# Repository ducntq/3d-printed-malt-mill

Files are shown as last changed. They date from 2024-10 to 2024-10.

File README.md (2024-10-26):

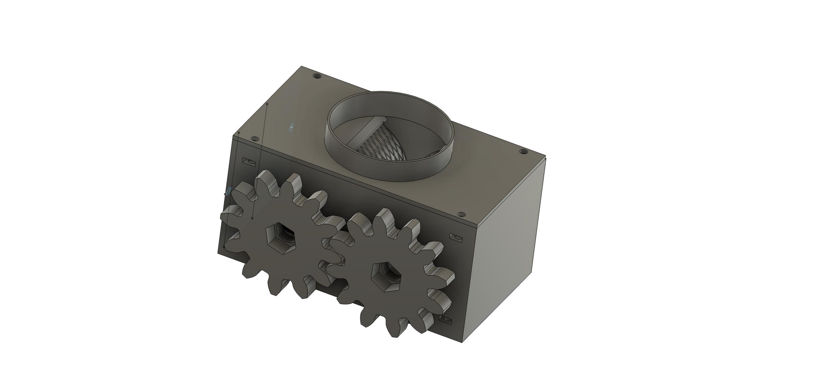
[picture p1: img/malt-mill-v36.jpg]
Malt Mill


# 3D Printer Malt Mill

I designed this malt mill from scratch but took inspiration from [https://github.com/xblax/3d_printed_malt_mill](https://github.com/xblax/3d_printed_malt_mill). I printed the malt mill by xblax, but I found several issues and limitations, ranging from the roller size too small to inconsistent use of screw thread sizes. So made several improvements:

1. Bigger rollers: meaning malt will get crushed easier, and malt will be fed to the rollers more easily as well.
2. Smaller gaps: reduce the chance of malt getting into gaps, which halt the operation of the mill.
3. Only M3 & M8: M3 screw for all structural connections, and M8 for the axles.

## Features

1. 50x50 rollers with 608 bearings
2. Adjustable gaps(1mm to 2.5mm)
3. Hopper attachment (please use the funnel designed by xblax as I haven't got the time to design my own [https://github.com/xblax/3d_printed_malt_mill/blob/master/stl/funnel_no_thread.stl](https://github.com/xblax/3d_printed_malt_mill/blob/master/stl/funnel_no_thread.stl))
4. Powered by cordless screwdriver

## BOM

You will need PLA or PETG, but I recommend to use PLA as it's food-safe.

### Non-printed parts

Item  | Quantity  | Purpose
------|-----------|---------
M8 Hex Socket Cap Screw, at least length 90 (recommended 100mm)| 2 | Axles
M3 Hex Socket Cap Screw, 25mm | 2 | Adjustment screws
M3 Hex Socket Cap Screwn, 14mm (max. 18mm) | 4 | Hopper attachment screws
M3 Hex Nut or Square Nut (both will work) | 6 | For screws' stability
M8 Hex Nut | 6 | 4 for rollers, 2 for gears

### Printed parts

Item | Quantity
-----|----------
Frame | 1
Rollers | 2
Gears | 2
Adapter | 1
Funnel | 1

## Printing guide

+ You probably will be fine with 10% in-fill, but I recommend at least 15%.
+ Frame should be printed upside-down.
+ Organic supports should be enabled everywhere.
+ Stars in-fill is recommended.
+ 3 perimeters, 3 top/bottom layers.

## License

The project is released under [MIT License](https://opensource.org/license/mit).

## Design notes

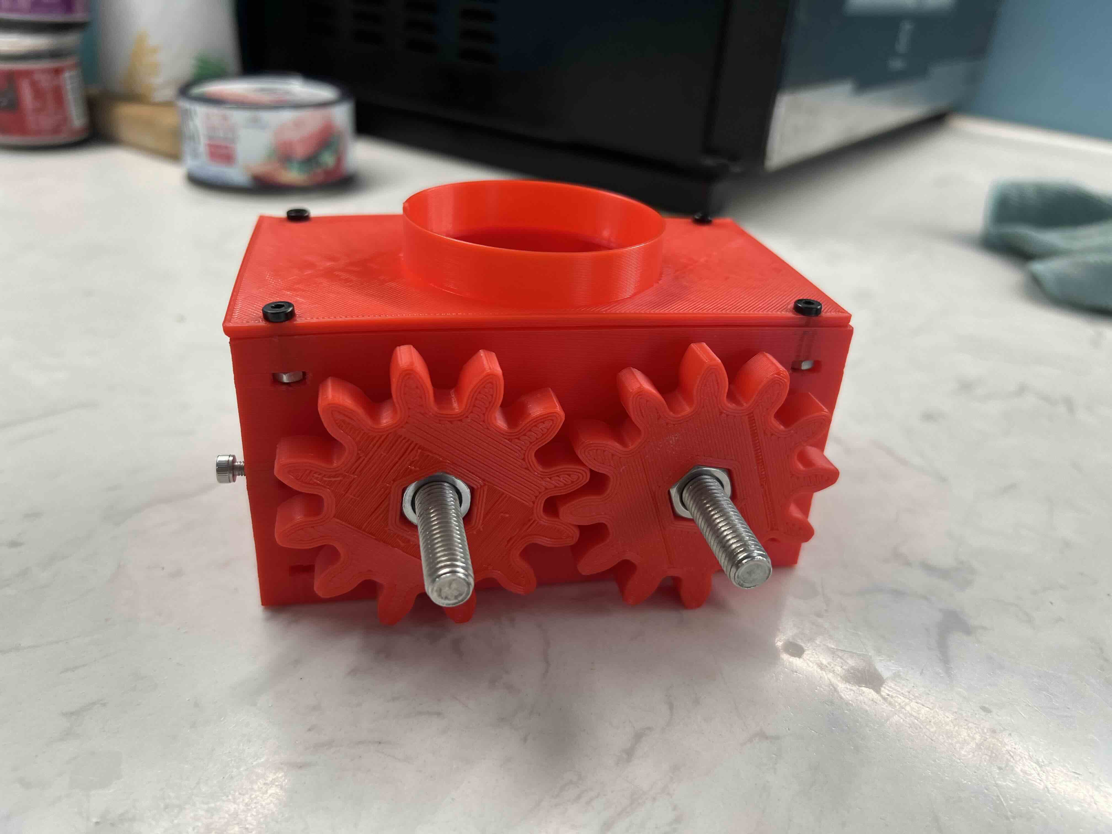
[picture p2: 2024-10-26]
img/back.jpg

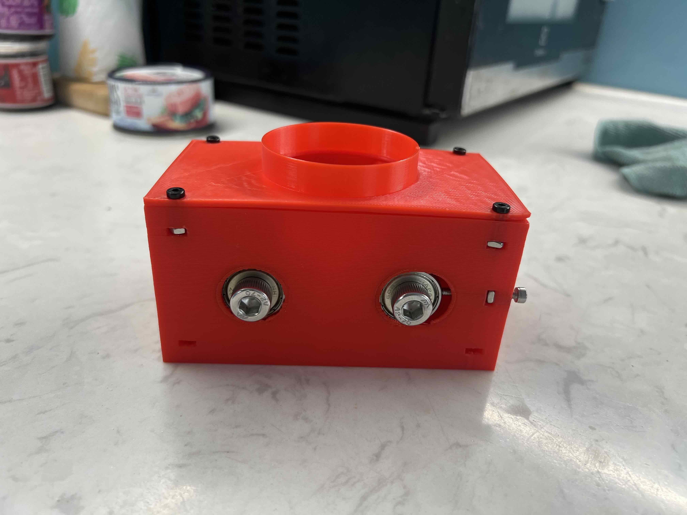
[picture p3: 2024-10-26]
img/front.jpg

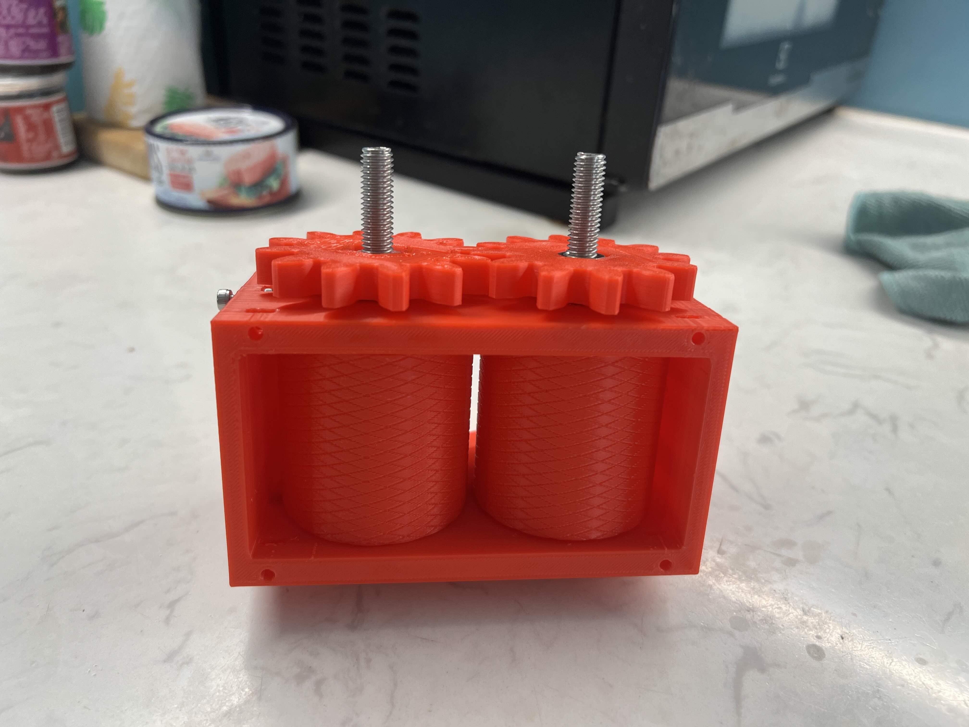
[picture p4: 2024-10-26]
img/bottom.jpg

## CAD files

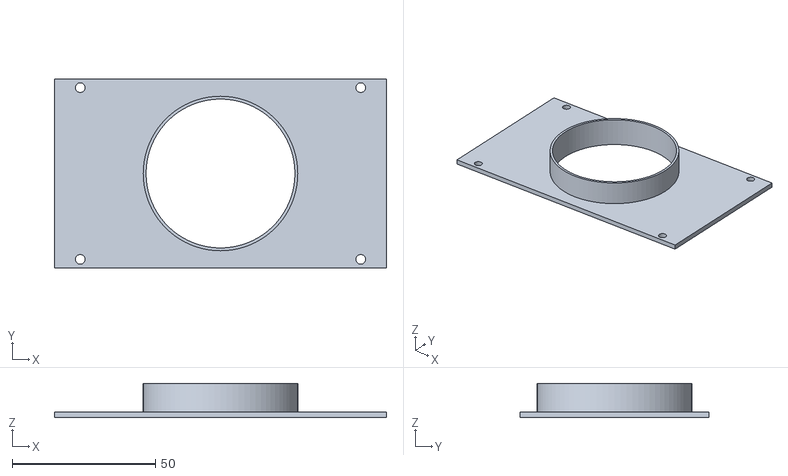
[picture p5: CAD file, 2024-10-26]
stl/Adapter.stl
116.0 x 66.0 x 12.0

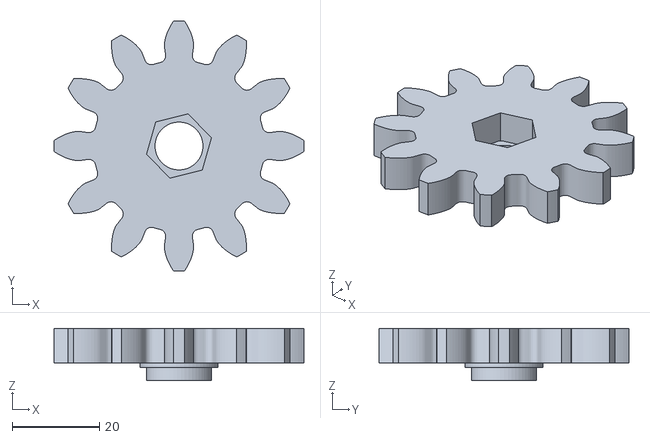
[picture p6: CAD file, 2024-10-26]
stl/Gear.stl
57.4 x 57.4 x 12.0

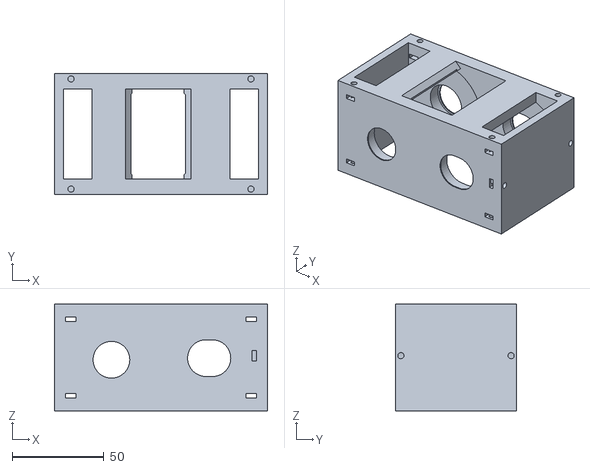
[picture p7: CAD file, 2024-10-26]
stl/Frame.stl
116.0 x 66.0 x 58.0

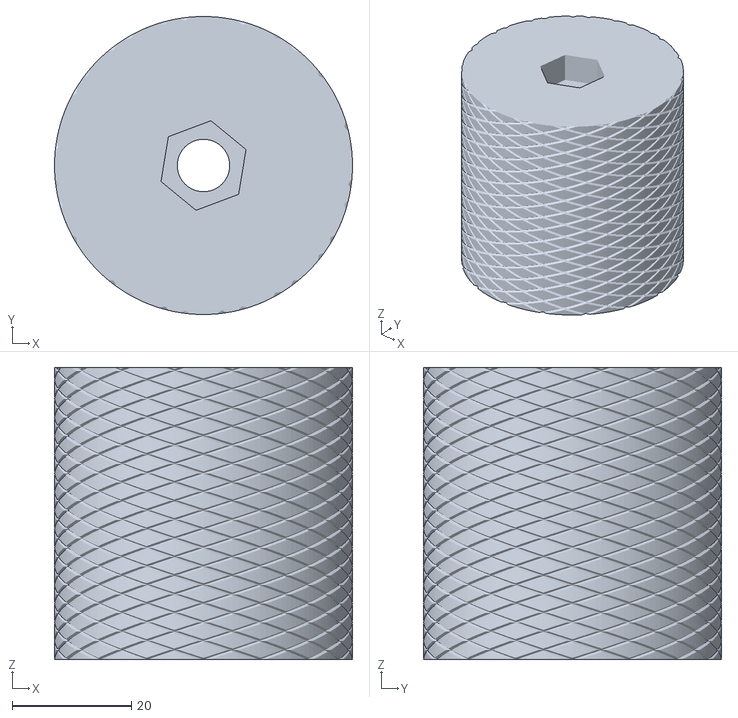
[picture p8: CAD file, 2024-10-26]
stl/Roller.stl
50.0 x 50.0 x 49.0

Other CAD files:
Malt Mill.f3d
